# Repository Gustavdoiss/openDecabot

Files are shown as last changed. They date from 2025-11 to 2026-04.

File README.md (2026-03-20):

# openDecabot
The easiest 3D printed robot you can assemble and program using Wemos D1 Mini Shields and Arduino IDE, powered by ESP8266. Made in Brazil, _Coisado no Ceará_.

**Assembly Instructions on WIKI http://github.com/triwaca/openDecabot/wiki**

Decabot robot on a Table
A hand holding a Decabot robot

## Hardware
### ESP8266 microcontroler
Open Decabot® uses the ESP8266 controler, in the Wemos Mini form factor, wich allows to use small shields to expand its capacities. In the simplest version, this robot uses a LED matrix shield and a custom connection shield, besides the Wemos D1 mini. The custom shield can be build with a PCB perfboard, a few pin header connections, and some soldering skills. 

By using the Espressif ESP8266 platform, the open Decabot® is nativelly equiped with Wi-Fi capabilities, allowing great IoT experiences, such as remote control and telemetry. 

More information about Wemos platform and a list of main shields available can be found on www.wemos.cc .

### Servo Motors
The open Decabot® robot uses two 360 servo motors to drive its wheels. It's the simplest solution for small robots, since the servo motors didin't require H bridge circuits (they already have those inside!) and can be connected directly to the ESP8266 pins. 

### 3D printed body
You can assemble your Open Decabot® using 3D printed parts. The basic chassis uses only 8 3D printed pieces, and can be assembled using a few screws. The 3D files can be found on **3dPrint** folder. 

### Simple AA batteries for power
Under the open Decabot® you can find a 4 x AA battery support, who can supply up to 6V directly to ESP board. This option simplifies the hardware, since the Wemos Mini board can hold the maxminum 6 volts, lowering the tension to 3 volts. Users can hack the project to use LiIon batteries, combined with the Wemos LiPo Battery Shield (https://www.wemos.cc/en/latest/d1_mini_shield/battery.html) for charging and step up the voltage to 5 volts. 

### Easy access to USB ports
There are two ports on the upper part of the robot who can be used to access the USB port (for firmware/Arduino sketch update), and other wiring and shield needs. 

Decabot robot conneceted using USB cable to a computer

### Bill of Materials - BOM
- 1 x Wemos D1 Mini ESP8266 controller
- 2 x Servo 5V 360
- 1 x Wemos LED Matrix Shield
- 1 x custom PCB board (check wiki how to build one) or 1 x Decabot Mini Shield PCB (see **/decabotMiniShield** folder)
- 1 x battery support for 4 x AA
- 1 x acrylic frontface + 2 hallen 3mm screws (optional)
- 7 x screws 3mm, 12mm long
- 2 x rubber o-ring for wheels, size 2" or 50mm (ref: DN50)
- 4 x AA batteries

### Decabot Mini Shield

#### Homemade PDB
Wemos platform does not have a simple shield board to connect servos, so you need a homemade board to use. It's goal is just to simplify the connection between the controller and the motors. A homemade PDB board can be assembled just to connect the main components to the Wemos board: Battery to 5V pin, and servos to D0 and D6 pins, as shown below:

Homemade Decabot Mini PCB

Homemade PCB circuit

#### Buy the Decabot Shield

Help funding this project by buying our dedicated shield. It is the easiest way to enjoy all the possibilities of your Open Decabot Robot!

- Easy access to Servo connections
- On-off switch
- Included buzzer for sounds
- Easy connection for extra sensors, such as line-folowing sensors
- Dedicated connection to Gyroscope/Accelerometer, for mapping projects
- Dedicated connection to I2C modules, such as OLED displays, distance sensors, RGB sensors and RFID/NFC sensors

Homemade PCB circuit

More information about commercial partnership on WIKI soon.

## Arduino Codes

The Arduino sketches can be found on **/ArduinoSketch** folder. You can simply copy this folder inside your Arduino folder on your computer, and open the `.ino` files. 

Remember that Decabot platform is based on `ESP8266` chip, in Wemos D1 Mini form factor. Your Arduino IDE must be proper set to manage ESP8266 family. To se if it is ready, go to `Tools` menu, then `Boards`, and look for `ESP8266 boards`. You must find `Wemos D1 Mini` there. If not, google for _installing ESP8266 on Arduino IDE_.

Some sketches uses libraries who must be installed before. See instructions on each sketch how to proceed. 

## 3D project source
The 3D source project was all designed on Tinkercad (yes!), and can be forked using the link below:
[https://www.tinkercad.com/things/cXxCpU8HWDP-opendecabot-mini-v13](https://www.tinkercad.com/things/cXxCpU8HWDP-opendecabot-mini-v13)

Decabot robot on Tinkercad

## Decabot® Trade Mark
Besides this project is open source, the Decabot® name is a registered trademark from Decano Kits Company, and should not be used without proper consent. 

## Open Source Licenses

Open Decabot® project is licensed under CC BY-NC-SA 4.0. You are free to:

- Share — copy and redistribute the material in any medium or format
- Adapt — remix, transform, and build upon the material

Under the following terms:

- Attribution — You must give appropriate credit , provide a link to the license, and indicate if changes were made . You may do so in any reasonable manner, but not in any way that suggests the licensor endorses you or your use.
- NonCommercial — You may not use the material for commercial purposes .
- ShareAlike — If you remix, transform, or build upon the material, you must distribute your contributions under the same license as the original.

https://creativecommons.org/licenses/by-nc-sa/4.0/

Creative Commons License By NC SA

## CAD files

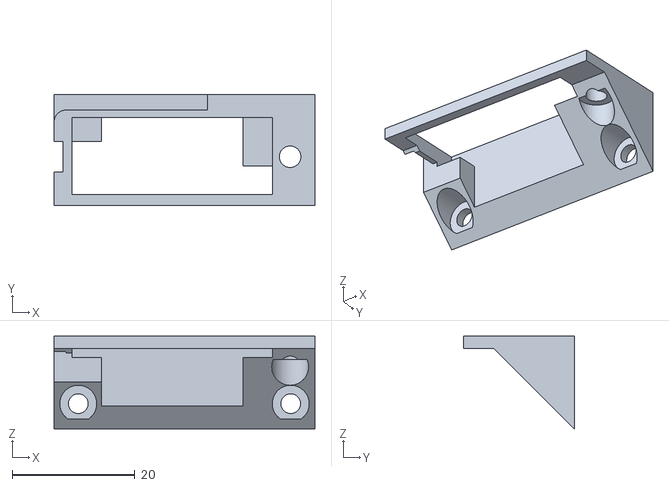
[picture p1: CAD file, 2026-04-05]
3dPrint/accessories/clawBase_OpenDecabotMINIV1.stl
42.5 x 18.0 x 15.1

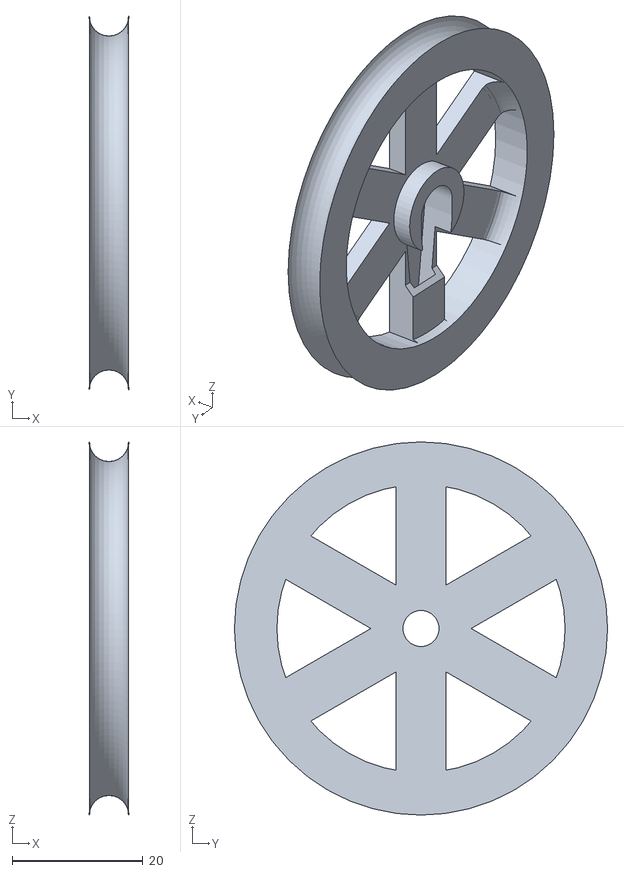
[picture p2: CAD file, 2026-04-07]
3dPrint/wheel_OpenDecabotMINIV1.stl
6.00 x 57.0 x 57.0

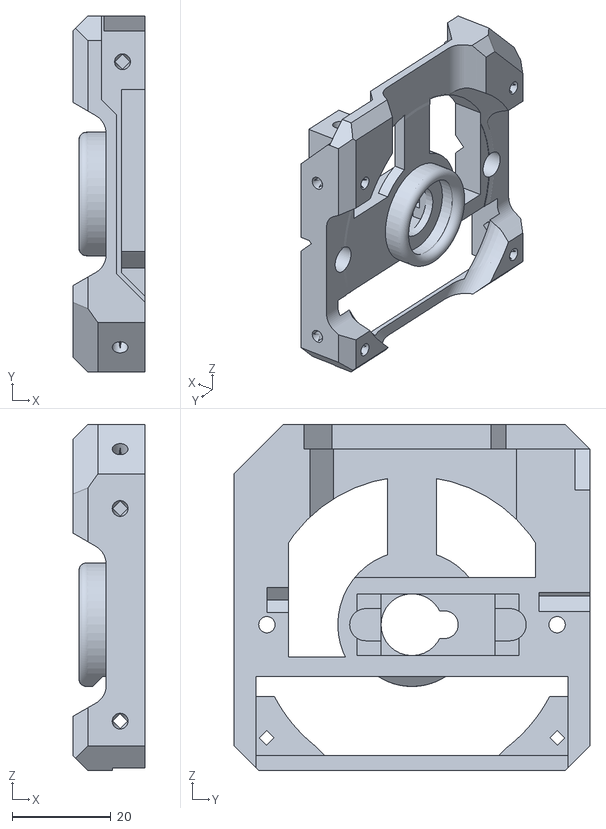
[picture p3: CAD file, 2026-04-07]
3dPrint/right_OpenDecabotMINIV1.stl
14.5 x 72.0 x 70.0

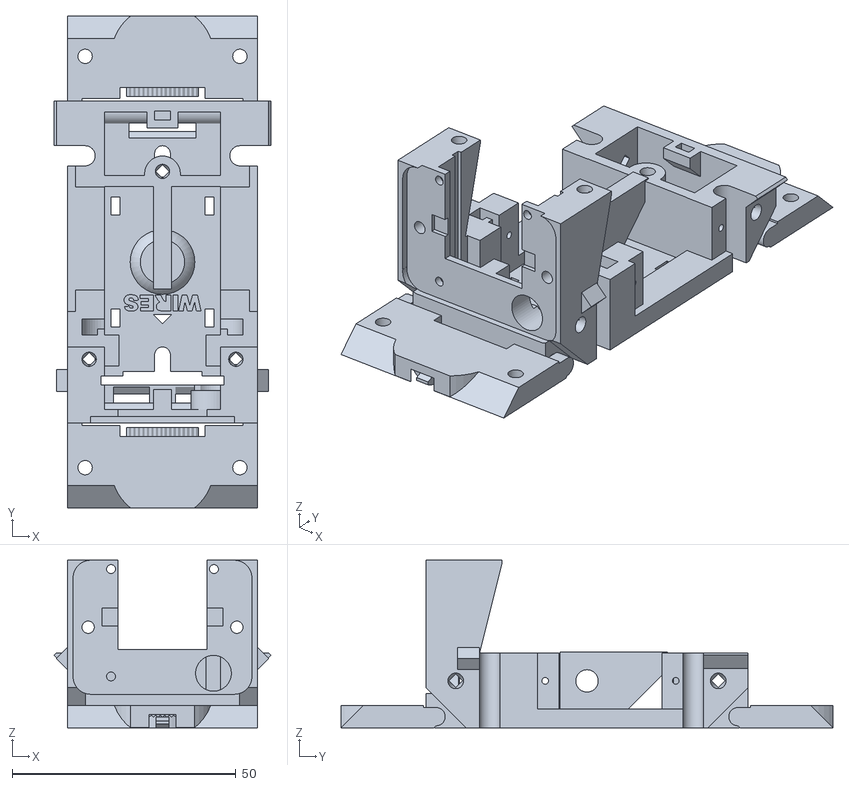
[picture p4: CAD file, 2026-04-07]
3dPrint/bottom_OpenDecabotMINIV1.stl
48.5 x 110.0 x 37.5

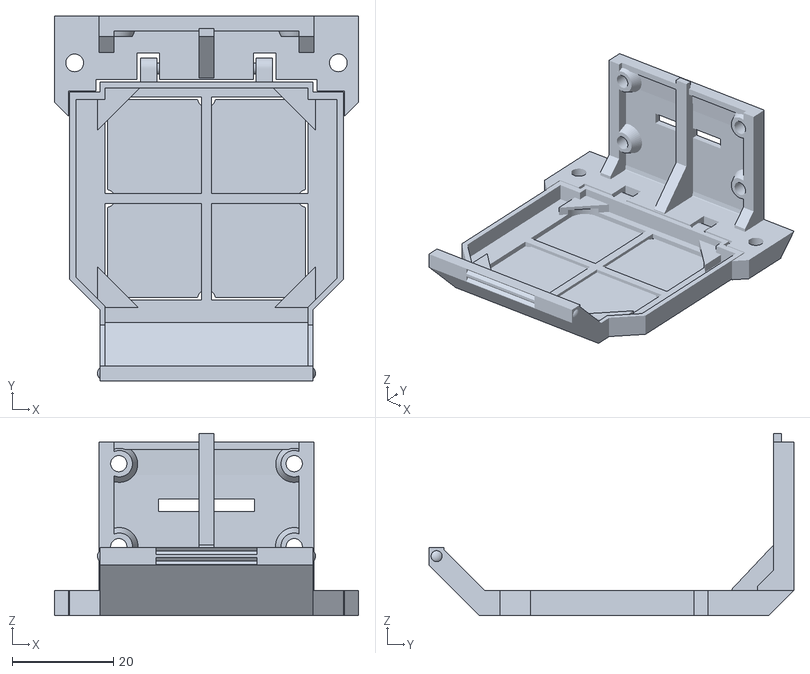
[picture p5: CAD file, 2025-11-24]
3dPrint/top_OpenDecabotMINIV1.stl
60.0 x 72.0 x 36.0

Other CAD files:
3dPrint/left_OpenDecabotMINIV1.stl

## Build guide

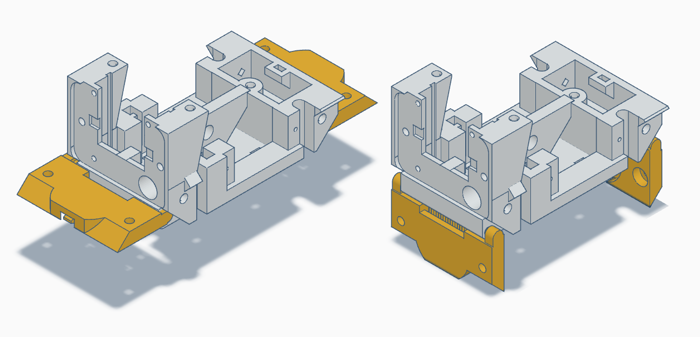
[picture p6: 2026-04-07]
images/montagemOpenDecabot_0.png

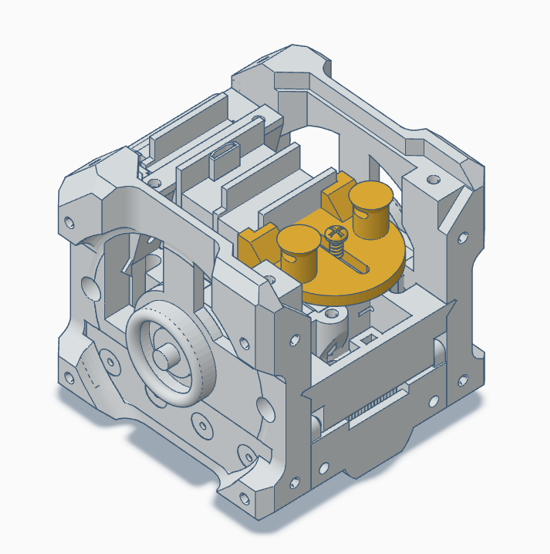
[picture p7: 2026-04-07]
images/montagemOpenDecabot_9.PNG

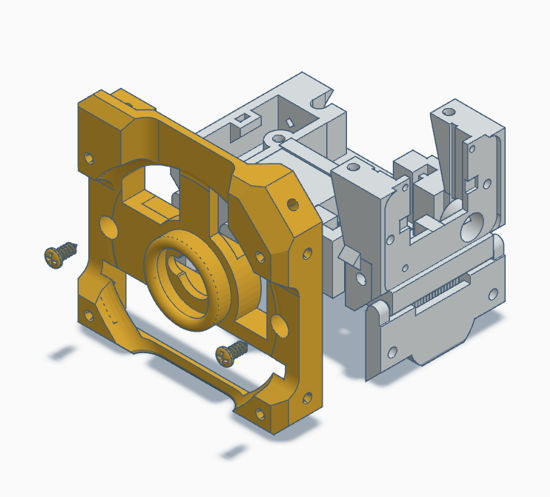
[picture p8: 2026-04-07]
images/montagemOpenDecabot_2.PNG

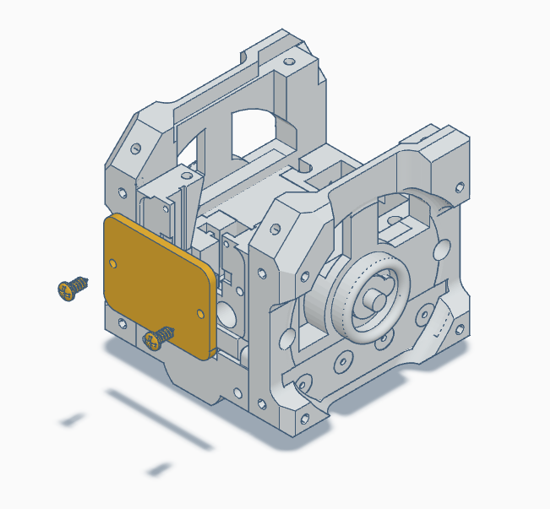
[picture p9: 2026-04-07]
images/montagemOpenDecabot_7.PNG

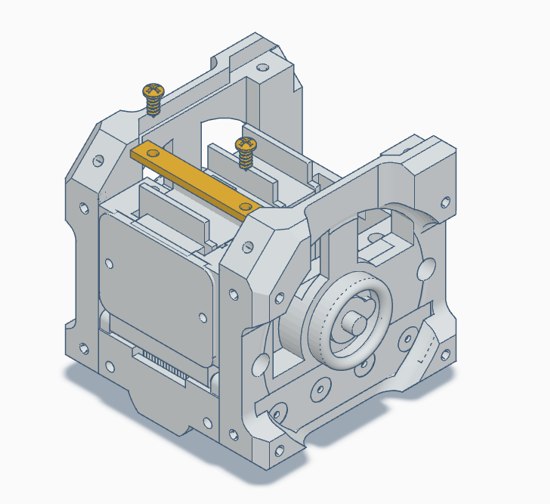
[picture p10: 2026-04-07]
images/montagemOpenDecabot_81.png

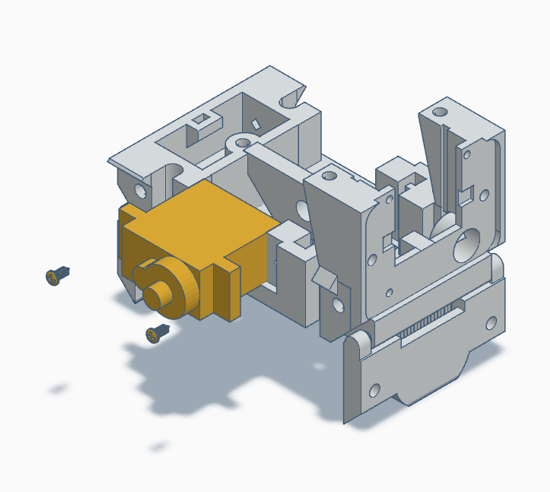
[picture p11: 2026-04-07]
images/montagemOpenDecabot_1.png

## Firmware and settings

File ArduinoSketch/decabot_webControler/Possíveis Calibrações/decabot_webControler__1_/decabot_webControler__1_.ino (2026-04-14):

/*
 * Captive Portal Decabot
 * Daniel Chagas, Nicole Akemi Takeda, Cauan Oliveira, Paulo Roberto Gomes
 *
 * Robô cria uma rede wifi com captive portal que exibe botões de controle
 * remoto que controlam os servo motores ligados às portas D0 (motor direito)
 * e D6 (motor esquerdo). 
 *
 * To use:
 * - Access the Wi-Fi network 'MeuDecabot' with a device such as smartphone,
 *   tablet or computer, and click on the login message. 
 * - You must see a page with a title and buttons who can control the movement
 * 
 * Hardware:
 * Wemos D1 Mini - https://www.wemos.cc/en/latest/d1/index.html
 * Matrix Led Shield - https://github.com/wemos/WEMOS_Matrix_LED_Shield_Arduino_Library
 * Decabot Mini Shield
 * 
 * PORTS                             _____________
 *                                  /             \
 *                             RST |*  ---------  *| TX 
 *           battery ---------- A0 |* |         | *| RX
 *         SERVO esq --GPIO16-- D0 |* |  ESP    | *| D1 ---I2C--- SCL
 *    led matrix CLK ---------- D5 |* |  8266   | *| D2 ---I2C--- SDA
 *         SERVO dir --GPIO12 - D6 |* |         | *| D3 --GPIO0-- SERVO
 *    led matrix DIN ---------- D7 |* |         | *| D4 --GPIO2
 *            buzzer --GPIO15-- D8 |*  ---------  *| GND
 *                             3V3 |*             *| 5V
 *                                  \              |
 *                            reset  |      D1mini |
 *                                    \___________/
 */


#include <ESP8266WiFi.h>
#include <ESPAsyncTCP.h>        //tested on 1.2.4 from https://github.com/dvarrel/ESPAsyncTCP
#include <ESPAsyncWebServer.h>  //tested on https://github.com/lacamera/ESPAsyncWebServer
#include <DNSServer.h>
#include <Servo.h>
#include <Adafruit_GFX.h>       // tested on 1.11.10
#include <WEMOS_Matrix_GFX.h>   // tested on 1.4.0iu332
#define buzzer D8

MLED matrix(7); // intensidade 7 (máximo)

int slowSpeed = 40; //number between 1 and 180 max.
int fastSpeed = 60; //number between 1 and 180 max.
//To vcalibrate motors: Positive mnumbers give more right movement
int calibration = 0; //number between -50 and 50 to balance motors

int lpos = 1; // posição olho esquerdo
int rpos = 6; // posição olho direito
int aleat = 5;

bool awake = false;

const char *ssid = "MeuDecabot";
const char *password = "";
Servo servo0;
Servo servo6;

//sounds
const int decabotMusic[4][3]{ { 494, 2, 3 }, { 554, 2, 4 }, { 440, 2, 5 }, { 880, 1, 6 } };
static const uint8_t PROGMEM decabotLogo[4][5] = {{0b11001110,0b10101000,0b10101100,0b10101000,0b11001110},{0b00110010,0b01000101,0b01000111,0b01000101,0b00110101},{0b11000100,0b10101010,0b11001010,0b10101010,0b11000100},{0b01110100,0b00100100,0b00100100,0b00100000,0b00100100}};


DNSServer dnsServer;
const byte DNS_PORT = 53;

AsyncWebServer server(80);

const int LED_PIN = LED_BUILTIN;
bool ledState = false;

void notFound(AsyncWebServerRequest *request) {
  request->redirect("/");
}

int neutralLeft  = 93;
int neutralRight = 93;

void motorLeft(int pot) {
  if (pot == 0) {
    servo0.write(neutralLeft);
  } else {
    int vel = neutralLeft + map(pot, -100, 100, fastSpeed, -fastSpeed);
    servo0.write(vel);
  }
}

void motorRight(int pot) {
  if (pot == 0) {
    servo6.write(neutralRight);
  } else {
    int vel = neutralRight - map(pot, -100, 100, fastSpeed, -fastSpeed);
    servo6.write(vel);
  }
}

void setup() {
  Serial.begin(115200);
  Serial.println();
  Serial.println();
  Serial.println("Decabot");
  pinMode(buzzer, OUTPUT);
  matrix.setRotation(2);
  servo0.attach(D0);
  servo6.attach(D6);
  Serial.begin(115200);

  pinMode(LED_PIN, OUTPUT);
  digitalWrite(LED_PIN, HIGH); // LED off (ativo em LOW)
  ledState = false;

  WiFi.mode(WIFI_AP);
  WiFi.softAP(ssid, password);
  IPAddress myIP = WiFi.softAPIP();
  Serial.print("AP IP address: ");
  Serial.println(myIP);

  dnsServer.start(DNS_PORT, "*", myIP);

  // Página raiz (cativa)
  server.on("/", HTTP_GET, [myIP](AsyncWebServerRequest *request) {
    awake = true;
    String ipStr = myIP.toString();
    String html = R"rawliteral(
<!DOCTYPE html>
<html lang="pt-BR">
<head>
  <meta charset="UTF-8" />
  <meta name="viewport" content="width=device-width, initial-scale=1" />
  <title>Controle do Robô</title>
  <style>
    :root{
      --bg:#1a1a2e;
      --btn:#16213e;
      --border:#0f3460;
      --txt:#fff;
      --accent:#0f3460;
    }
    *{box-sizing:border-box}
    html,body{
      height:100%;
      margin:0;
    }
    body {
      background: var(--bg);
      font-family: Arial, Helvetica, sans-serif;
      color: var(--txt);
      display: flex;
      flex-direction: column;
      justify-content: center;
      align-items: center;
      gap: 18px;
      user-select: none;
      -webkit-user-select: none;
    }

    .calibrador {
      text-align: center;
      margin-top: 10px;
    }

    h1{margin:0 0 4px 0;font-size:20px;opacity:.9}
    .controle {
      display: grid;
      grid-template-columns: 90px 90px 90px;
      grid-template-rows: 90px 90px 90px;
      gap: 14px;
      touch-action: none; /* evita scroll durante o toque */
    }
    button {
      background: var(--btn);
      color: var(--txt);
      border: 2px solid var(--border);
      border-radius: 16px;
      font-size: 22px;
      cursor: pointer;
      transition: transform .08s ease, background .15s ease;
      outline: none;
      -webkit-tap-highlight-color: transparent;
    }
    button:active{
      transform: scale(0.97);
      background: var(--accent);
    }
    /* posição dos botões */
    .frente  { grid-column: 2; grid-row: 1; }
    .esquerda{ grid-column: 1; grid-row: 2; }
    .direita { grid-column: 3; grid-row: 2; }
    .tras    { grid-column: 2; grid-row: 3; }

    .status{
      font-size:14px;
      opacity:.85;
    }

    @media (max-width: 420px){
      .controle{
        grid-template-columns: 80px 80px 80px;
        grid-template-rows: 80px 80px 80px;
        gap: 12px;
      }
    }
  </style>
</head>
<body>
  <h1>Controle do Robô</h1>

  <div class="controle">
    <button class="frente"   aria-label="Frente"   onpointerdown="press('Front')" onpointerup="release()" onpointerleave="release()">▲</button>
    <button class="esquerda" aria-label="Esquerda" onpointerdown="press('Left')"  onpointerup="release()" onpointerleave="release()">◄</button>
    <button class="direita"  aria-label="Direita"  onpointerdown="press('Right')" onpointerup="release()" onpointerleave="release()">►</button>
    <button class="tras"     aria-label="Trás"     onpointerdown="press('Back')"  onpointerup="release()" onpointerleave="release()">▼</button>
  </div>

  <div class="calibrador">
    <span>Calibração: <strong id="valorCalib" class="valorCalib">0</strong></span>
    <br>
    <input id="calibBarra" type="range"  min="-50" max="50" value="0" onchange="newCalibration(this.value)" oninput="changeCVT(this.value)">
  </div>

  <div class="status">LED status: <strong id="ledState">unknown</strong></div>
  <a href="http://)rawliteral" + ipStr + R"rawliteral(/" style="color:#9bd">Abrir no navegador</a>

  <script>
    let isPressed = false;

    function changeCVT(value) {
      const textCalib = document.getElementById('valorCalib');
      textCalib.innerHTML = value;
    }

    function newCalibration(value) {
      return fetch('/calibrar?val=' + value)
        .catch(() => {});
    }

    function setLED(state) {
      return fetch('/led?state=' + state)
        .then(r => r.text())
        .then(text => {
          const el = document.getElementById('ledState');
          if (el) el.textContent = text;
        })
        .catch(() => {});
    }

    function press(direction){
      if (isPressed) return;
      isPressed = true;
      setLED(direction);
    }

    function release(){
      if (!isPressed) return;
      isPressed = false;
      setLED('Stop'); // volta para neutro ao SOLTAR
    }

    function getLEDStatus() {
      fetch('/status')
        .then(r => r.text())
        .then(text => {
          const el = document.getElementById('ledState');
          if (el) el.textContent = text;
        })
        .catch(() => {});
    }

    // Se sair da aba, solta os botões
    window.addEventListener('blur', release);
    // Estado inicial
    window.onload = getLEDStatus;
  </script>
</body>
</html>
    )rawliteral";

    request->send(200, "text/html", html);
  });

  // Comandos: Front / Left / Right / Back / Stop
  server.on("/led", HTTP_GET, [](AsyncWebServerRequest *request) {
    if (request->hasParam("state")) {
      String state = request->getParam("state")->value();

      if (state == "Front") {
        digitalWrite(LED_PIN, LOW);
        ledState = true;
        motorLeft(100);
        motorRight(100);
      } else if (state == "Left") {
        digitalWrite(LED_PIN, LOW);
        ledState = true;
        motorLeft(50);
        motorRight(-50);

      } else if (state == "Right") {
        digitalWrite(LED_PIN, LOW);
        ledState = true;
        motorLeft(-50);
        motorRight(50);

      } else if (state == "Back") {
        digitalWrite(LED_PIN, LOW);
        ledState = true;
        motorLeft(-50);
        motorRight(-50);

      } else if (state == "Stop") {
        digitalWrite(LED_PIN, HIGH);
        ledState = false;
        motorLeft(0);
        motorRight(0);

      } else {
        request->send(400, "text/plain", "Invalid state");
        return;
      }

      request->send(200, "text/plain", ledState ? "ON" : "OFF");
    } else {
      request->send(400, "text/plain", "Missing parameter");
    }
  });

  server.on("/status", HTTP_GET, [](AsyncWebServerRequest *request) {
    request->send(200, "text/plain", ledState ? "ON" : "OFF");
  });

  server.onNotFound(notFound);

  // Calibração do Decabot
  server.on("/calibrar", HTTP_GET, [](AsyncWebServerRequest *request) {
    if (request->hasParam("val")) {
        String valorString = request->getParam("val")->value();
        calibration = valorString.toInt();

        Serial.print("Nova calibracao: ");
        Serial.println(calibration);

        request->send(200, "text/plain", "Calibrado com sucesso!");
    }else {
        request->send(400, "text/plain", "Parâmetro ausente");
    }
  });

  server.begin();
  for (int i = 0; i < 4; i++) {
    matrix.clear();
    matrix.drawBitmap(0, 2, decabotLogo[i] , 8, 5, LED_ON);
    matrix.writeDisplay();
    tone(buzzer, decabotMusic[i][0], decabotMusic[i][1] * 200);
    delay(decabotMusic[i][1] * 200);
    noTone(buzzer);
  }
  delay(500);
  matrix.clear();
}

void loop() {
  dnsServer.processNextRequest();

  if(awake){
    // animação dos olhos + buzzer (mantida)
    matrix.clear();
    matrix.drawLine(lpos, 2, lpos, 7, LED_ON);
    matrix.drawLine(rpos, 2, rpos, 7, LED_ON);
    matrix.writeDisplay();
    delay(1000);

    // efeito de piscar
    for (int j = 0; j < random(3); j++) {
      for (int i = 2; i < 7; i++) {
        matrix.clear();
        matrix.drawLine(lpos, i, lpos, 7, LED_ON);
        matrix.drawLine(rpos, i, rpos, 7, LED_ON);
        matrix.writeDisplay();
        digitalWrite(buzzer, HIGH);
        delay(15);
        digitalWrite(buzzer, LOW);
        delay(15);
      }
      for (int i = 7; i > 2; i--) {
        matrix.clear();
        matrix.drawLine(lpos, i, lpos, 7, LED_ON);
        matrix.drawLine(rpos, i, rpos, 7, LED_ON);
        matrix.writeDisplay();
        digitalWrite(buzzer, HIGH);
        delay(15);
        digitalWrite(buzzer, LOW);
        delay(15);
      }
    }
  
    // olhar para os lados
    aleat = random(10);
    if (aleat < 2) {
      lpos = 0;
      rpos = 5;
    } else if (aleat > 7) {
      lpos = 2;
      rpos = 7;
      delay(15);
    } else {
      lpos = 1;
      rpos = 6;
      delay(15);
    }
  } else {
    matrix.drawLine(0, 7, 2, 7, LED_ON);
    matrix.drawLine(5, 7, 7, 7, LED_ON);
    matrix.writeDisplay();
  }
}

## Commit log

2025-11-24 Update on 3D parts for accessories
    Included option to receive ESPCAM as micrcontroller
    [bottom_OpenDecabotMINIV1.stl, top_OpenDecabotMINIV1.stl]
2026-04-05 Update clawBase_OpenDecabotMINIV1.stl
    More space to servo cable, avoiding bending too much
    [clawBase_OpenDecabotMINIV1.stl]
2026-04-07 Upgrade on 3D parts
    Inlcuded holes for servo screws, external holes for future expansions. New format of bottom chassis allows fix PCBs with secure (with new piece).
    [bottom_OpenDecabotMINIV1.stl, left_OpenDecabotMINIV1.stl, right_OpenDecabotMINIV1.stl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]
2026-04-07 New assembling images
2026-04-14 Altered fast/slow speed and 0rpm angle
    Slow Speed = 40;
    Fast Speed = 60;
    Resting Angle = 93º;
2026-04-14 Solução do Desvio para a direita
